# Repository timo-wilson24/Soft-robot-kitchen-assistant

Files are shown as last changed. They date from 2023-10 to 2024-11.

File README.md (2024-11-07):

# Soft-robot-kitchen-assistant
This is a repository for the code, CAD and assembly information for the 'Soft Robotic Kitchen Assistant for People with a Fine Motor disability' project I completed. 

The project addresses the challenge of food preparation for individuals with fine motor control difficulties or limb amputations by providing a dual-mode (soft and rigid) robotic device. The device uses a PneuNet based 'finger' actuator designed for finer slicing and rigid second system with some compliance. The innovation extends the applications of soft robotics and facilitates independent living for individuals with disabilities and showcasing the synergy between pneumatic rigid and compliant robotics in enhancing daily tasks. 

## Videos of Project:
- AUSSEF - Chopping Board Assistant Submission Video (recommended): https://youtu.be/T2KDRH2tRoQ?si=e9xJF4VDxiq_ELAp
- Soft Robotics Toolket Competition - Soft Robotic Chopping Board Assistant Submission Video: https://youtu.be/luMKAHcBeGc?si=Hu5qlbttlR9tySVy
- Young Scientist - Chopping Board Assistant Video: https://youtu.be/AkrwtVQIluE?si=esvOkE4GFkxM-J67

## Research Documentation
[Research documentation](Research%20Documentation/) has been formally published to the Harvard Soft Robotics Toolkit website and this repository. See
[AUSSEF Research Documentation](/Research%20Documentation/Research%20Documentation/AUSSEF%20Submission%20-%20chopping%20board%20innovation.pdf)
and
[SRT Competition Documentation](Research%20Documentation/Soft%20robotic%20kitchen%20assistant%20-%20SRT%20Submission.pdf)

## Competition Results
- 1st place in the College Category for the [Harvard Soft Robotics Competition 2023](https://softroboticstoolkit.com/competitions/2023#)
- 3rd place in the Technological Innovations Y11-12 Category at the [STANSW Young Scienist Awards 2023](https://viewer.joomag.com/2023-stansw-ysa-presentation-ceremony-booklet/0514268001701144660/p31)
- 2nd Place AARNet Use of Technology Award - Secondary ([at the STANSW Young Scientist Awards 2023](https://viewer.joomag.com/2023-stansw-ysa-presentation-ceremony-booklet/0514268001701144660/p41))

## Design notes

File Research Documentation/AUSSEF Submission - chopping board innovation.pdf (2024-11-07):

# DESIGN METHODOLOGY FOR A SOFT ROBOTIC INNOVATION: ADVANCING KITCHEN INDEPENDENCE AMONG INDIVIDUALS WITH FINE MOTOR DISABILITIES

## An Engineering Research and Development Project

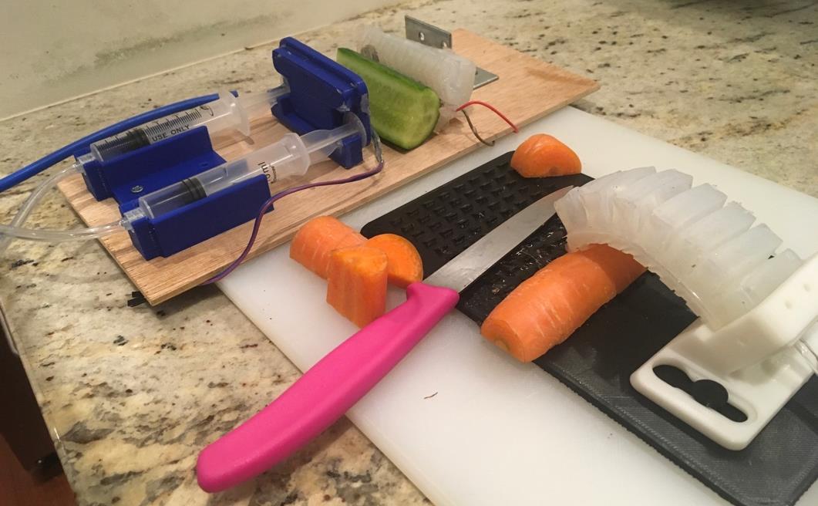
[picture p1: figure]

1. RESEARCH PROBLEM | 2
1.1. DESCRIBES A PRACTICAL NEED OR PROBLEM TO BE SOLVED IN LIGHT OF PRIOR ATTEMPTS OR SOLUTIONS | 2
1.2. EXPLORED EXISTING IDEAS AND ALTERNATIVES | 5
1.3. IDENTIFIES THE SIGNIFICANCE OF A SOLUTION FOR SOCIETY | 7
1.4. DEFINES THE CRITERIA FOR A PROPOSED SOLUTION | 7
2. DESIGN AND METHODOLOGY | 9
2.1. EXHIBITS A WELL-CONSTRUCTED PLAN TO ADDRESS THE NEED OR PROBLEM | 9
2.2. JUSTIFIES THE CHOICE OF MATERIALS AND TECHNOLOGIES SELECTED | 10
2.3. DESCRIBES A PROPOSED PROTOTYPE OR MODEL TO DEMONSTRATE THE SOLUTION | 12
2.4. DEMONSTRATES DEPTH OF UNDERSTANDING OF TECHNOLOGICAL METHODOLOGY USED. | 16
3. EXECUTION: CONSTRUCTION AND TESTING OF A PROTOTYPE | 19
3.1. EXHIBITS GOOD DESIGN AND PRODUCTION SKILLS | 19
3.2. HAS BEEN TESTED IN MULTIPLE CONDITIONS AND OR TRIALS | 33
3.3. USES AN APPROPRIATE APPLICATION OF MATHEMATICAL AND SCIENTIFIC METHODS | 37
3.4. DEMONSTRATES ENGINEERING SKILL TO DEVELOP A RELIABLE AND FUNCTIONAL SOLUTION | 38
4. CREATIVITY OR INNOVATION | 38
SIGNIFICANT CREATIVITY AND OR INNOVATION SHOWN IN ONE OR MORE OF THE ASPECTS OF THE PROJECT | 38
5. CONCLUSION AND DISCUSSION | 41
5.1. EVALUATES THE POTENTIAL IMPACT OF THE PROTOTYPE OR MODEL FOR ENGINEERING, AND/OR FOR SOCIETY | 41
5.2. DEMONSTRATES UNDERSTANDING, INTERPRETATION AND LIMITATIONS OF THE PRODUCT/SOLUTION | 42
5.3. DEMONSTRATES DEPTH OF UNDERSTANDING IN RELEVANT CONCEPTS, STRUCTURES AND PROCESSES | 42
5.4. SUGGESTS MEANINGFUL AND RELEVANT IDEAS FOR FURTHER RESEARCH AND DEVELOPMENT | 43
6. PRESENTATION AND COMMUNICATION | 44
6.1. ADDRESSES PURPOSE AND AUDIENCE | 44
6.2. DEMONSTRATES LOGICAL ORGANISATION OF MATERIAL | 45
6.3. HAS CLEARLY ILLUSTRATED INITIAL IDEAS AND ALL DESIGN STAGES TO THE FINAL DESIGN | 45
6.4. PROVIDES EVIDENCE OF A HIGH DEGREE OF INDEPENDENCE OF THE STUDENT | 45
7. EVIDENCE OF PROJECT, MEDIA OF FINAL PRODUCT | 45
7.1. VIDEO: | 45
7.2. OTHER PHOTOS OF PRODUCT: | 46
7.3. CAD, ENGINEERING DRAWINGS | 48
8. REFERENCES | 48

## 1. Research Problem

1.1. Describes a practical need or problem to be solved in light of prior solutions
Independence is an important part of adult life. As people get older, being independent becomes more difficult due to the effects of aging. Similarly, people with a disability define being independent as their key need in life. Independence is empowering and important for physical and mental health long-term. This project strives to enable people to obtain independence, allowing individuals to remain in their home environment by being able to prepare food at home, which is a core element to being independent.

Preparing and cooking food can be a significant challenge
for many individuals who face difficulties with fine motor
control, despite the availability of accessible cooking options. The process of preparing a healthy meal often involves precise and delicate slicing of various ingredients, each presenting unique challenges based on their texture and hardness, whether they are slippery, hard, small, or soft. Consequently, individuals with limited fine motor skills, or those with amputations that clearly result in a complete lack of fine motor control in one limb, often encounter obstacles that hinder their ability to prepare food in a manner similar to that of able-bodied individuals. See examples of conditions that can significantly affect someone’s independence on the right.

At present, many national populations around the world are aging. This means that in the future the number of people requiring assistance due to age-related illnesses is likely to increase. This has far-reaching implications and will require more assistive technology to be developed so people can continue to live on their own and not rely on carers through governmental social welfare (as there will

be too many people making it unsustainable). A demographic pyramid of Australia’s asymmetrical aging population is below.

Figure 4: Australian Demographics Data¹

1 Australia Age structure - Demographics (indexmundi.com) (https://www.indexmundi.com/australia/age_structure.html)

Figure 1: Rheumatoid arthiritis of the hands on an elderly individual

Figure 2: Finger amputation due to accident

Figure 3: Hand spasticity

An inability to prepare healthy and nutritious food (i.e., not being able to chop, slice fruit or vegetables) can have detrimental effects on diet and an individual’s sense of independence. Research on individuals who don’t (or cannot) cook for themselves demonstrates that, “Those eating home cooked meals more than five times, compared with less than three times per week, consumed 62.3 g more fruit (99% CI 43.2 to 81.5) and 97.8 g more vegetables (99% CI 84.4 to 111.2) daily. More freque nt consumption of home cooked meals was associated with greater likelihood of having normal range BMI and normal percentage body fat. … Those consuming home cooked meals more than five times, compared with less than three times per week, were 28% less likely to have overweight BMI (99% CI 8 to 43%), and 24% less likely to have excess percentage body fat (99% CI 5 to 40%).”²

It is well established that having a healthy and nutritious diet affects long term physical and mental health and is an important way of staying healthy for everyone³
. People with a disability are at a much higher risk of being affected by a poor diet⁴
, “Based on self-reported data, around half (47%) of people aged 2 and over with disability eat less than the recommended serves of fruit and less than the recommended serves of vegetables each day, and are more likely than people without disability (41%) to not meet the guidelines”⁵⁶
. This is a problem which endemically impacts, “Younger adults with disability are more likely than older adults with disability not to eat enough fruit or vegetables each day. Around half (53%) of younger adults (aged 18–64) with disability eat less than the recommended serves of fruit or vegetables each day, compared with 39% of older people [aged over 65] with disability.”⁷

At present, the market offers limited solutions to address the challenge of preparing fresh produce for individuals with fine motor control difficulties, and unfortunately, accessibility remains a significant concern. These existing solutions, with the notable exception of food processors, predominantly consist of passive devices like spikes and flexible clamps. However, their applicability is far from universal, as they often fall short in effectively accommodating the diverse array of culinary tasks and the wide range of fruits and vegetables encountered in daily meal preparation. Additionally, many of the existing devices require the use of sharp spikes, or other guides which require the knife to be close to the hand, increasing risk of injury. There is limited academic research The need for an innovative and comprehensive solution that caters to a broader spectrum of disabilities and culinary needs becomes apparent in this context.

2 Mills S, Brown H, Wrieden W, White M, Adams J. Frequency of eating home cooked meals and potential benefits for diet and health: cross-sectional analysis of a population-based cohort study. Int J Behav Nutr Phys Act. 201.

3 Siefert, K., Heflin, C. M., Corcoran, M. E., & Williams, D. R. (2004). Food Insufficiency and Physical and Mental Health in a Longitudinal Survey of Welfare Recipients. Journal of Health and Social Behavior, 45(2), 171–186.

4 “People with Disability in Australia, Health Risk Factors and Behaviours,” Australian Institute of Health and Welfare, July 5, 2022.

5 ABS (Australian Bureau of Statistics) (2018a) National Health Survey: first results, 2017–18, (http://www.abs.gov.au/statistics/health/health-conditions-and-risks/national-health-survey-first-results/latest-release) ABS cat. no. 4324.0.55.001, ABS.

6 ABS (2018b) ABS sources of disability information, 2012–2016, (http://www.abs.gov.au/ausstats/abs@.nsf/mf/4431.0.55.002) ABS cat. no. 4431.0.55.002, ABS.

7 ABS (2019) Microdata: National Health Survey, 2017–18, (https://www.abs.gov.au/statistics/microdata-tablebuilder/available-microdata-tablebuilder/national-health-survey) ABS cat. no. 4364.0.55.001, ABS, AIHW analysis of the main unit record file (MURF).

Aside from the clear social significance of my need, the device also contributes to current research on soft robotics by providing a comparison with a rigid robotic system (the clamp) and a soft system. My invention also provides yet another effective use case, with a clear methodology for others to follow. Soft robotics is a new field that integrates compliant and flexible materials into the design and fabrication of robots, offering advantages in safety⁸

, adaptability, and versatility⁹ . An example of
a soft robot is seen in Figure 5 below. These characteristics align perfectly with the requirements of my project, which seeks to provide a user-friendly, adaptable, and effective solution for individuals with disabilities that gives them independence to prepare food. By incorporating soft robotics principles, I aim to create a gripper that not only enhances accessibility but also contributes to the evolving landscape of assistive technology, particularly in applying these technologies to improve the quality of life for individuals with disabilities.

Figure 5: Soft robot

1.1.1. Design Situation
Many individuals with limited fine motor skills or amputations face difficulties when cooking and preparing food in the kitchen, especially to do with the chopping/slicing of fresh produce. Having a fine motor disability also greatly increases the risk of an accident in the kitchen because their grip on objects is often unstable or insufficient. This also impacts people with arm or hand amputations. It is important that people with a disability have access to tools which allow them to be independent and cook healthy, homemade food themselves.

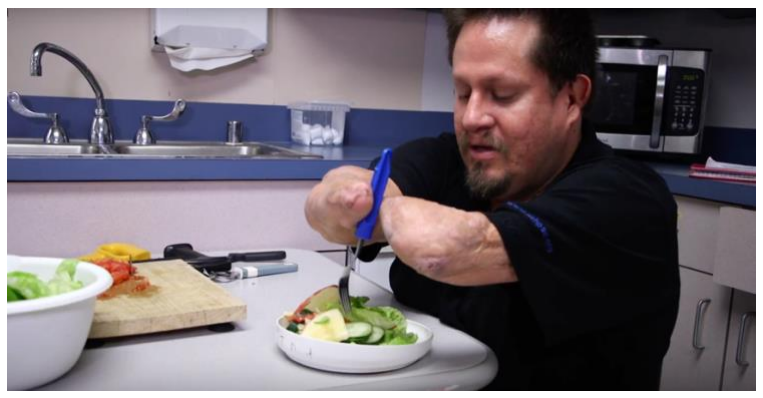
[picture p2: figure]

Figure 6: An individual with lower arm amputations making a salad. Source: YouTube

8 Haider Abidi and Matteo Cianchetti, “On Intrinsic Safety of Soft Robots,” Frontiers in Robotics and AI 4 (February 20, 2017).

9
Jun Shintake et al., “Soft Robotic Grippers,” Advanced Materials 30, no. 29 (May 7, 2018): 1707035.

1.1.2. Design Brief
Design a product which assist people with a fine motor disability to hold their fresh produce for chopping or slicing, aiming to enhance the user’s independence and effectiveness in food preparation, ensuring their safety.
1.2. Explored existing ideas and alternatives
1.2.1. Existing Product Research
To analyse existing products and solutions, I decided to research the products in categories, and ignore any duplicated products with similar conceptual design implications.
Solution 1: Safety Chopping Board Tool
- Requires two hands to use, still needs 1 hand to close the
boards holding the vegetable.
- Vegetable can still move in device (based on how hard the user is holding)
+ Very safe, well-protected
+ Easy to clean
+ Aesthetically unexciting
Target Market: elderly, those with Parkinson’s, people with limited strength, want safety.

Solution 2: Adaptive Cutting Board - Multiple devices
- Effective at holding soft objects, difficult for harder objects.
- Spikes dangerous for user
+ Good adjustability but requires some fine motor skills to move.
+ Holds most sizes of objects
+ Good modularity for future tools
+ Well planned aesthetically
Target Market: Very open to all disabilities, or people with issues prepping food. Less advertised to non-disabled audience.

Solution 3: Food Slicer Assistant - prongs

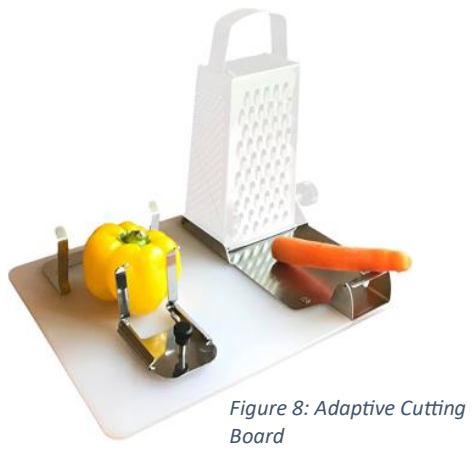
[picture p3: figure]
Figure 8: Adaptive Cutting Board

- Rounded, small diameter handle – is it able to be gripped even with a fine motor condition?
- Potential safety issue of sharp prongs
- Hard to push into the vegetable
- Only applicable to a small range of fruit/vegetables
+ Can cut between prongs and close to prongs, allowing finer slicers with safety issues
+ Very stable, little risk of fruit, hand slipping.
+ Cheap (can be found for less than $10)
Target Market: Open to the non-disabled audience, maybe chefs, or cooks generally not as good at cutting.

Figure 7: Safety Chopping Board, Source: Pinterest

Source: AliExpress.com

Solution 4: Food Processor
- Difficult to detach bowl with lid from processor
- Blades spin fast, are a little dangerous to change, clean, and put food in if you have limited fine motor
- Limited ability to slice food to a specified size.
- Decreases independence as it does it all for you
+ Handle (accessible)
+ Easy to turn on and slice
+ Does not require strength to chop (does it for you)
Target Market: Broadly accessible to all who want to get kitchen tasks done faster, and the ability to automate chopping tasks (when the user doesn’t care about precision in cutting).

Solution 5: Chopping 'Pegboard' Prototype
- Cannot hold with much force, only rest vegetables against
- Difficult to clean inside pegs.
- Requires decent fine motor skills to put in 'pegs’.
+ Adjustability for many use cases
+ Knife, utensil storage

Solution 6: Prototype 'Gear' Cutting Board
- Not much ability to hold harder vegetables like carrot.
- Product does not use a material that is easily gripped
- Cleaning is difficult.
+ Great for herbs, leafy greens as they are pushed with gears. + Operation of gears can be done with body (not hand)
1.2.2. Summary of market research

There are a few products which have been designed to assist people with the preparation of food. The current best option for people to hold while they cut vegetables is Solution 2. The solution allows individuals to use the device one handed, but it still requires a decent amount of dexterity to set up. Most user’s who require this product are going to have limited dexterity. However, this solution is not able to cater to a very large range of sizes of fruits and vegetables as well as hardness. This might mean that larger vegetables such as capsicum can’t be cut. Other solutions often necessitate the use of a second hand to use or to set up. This means that the device is not accessible for people with amputations to an arm, or stroke victims who cannot use an arm.
On the whole, the market while offering some solutions does not offer a clear solution that is adaptable to the larger target market. Furthermore, individuals with more severe fine motor disabilities are still disadvantaged significantly with most of the solutions as the operation of the device requires dexterity.

Figure 10: Common Food Processor

Figure 11: Chopping
Board 'Pegboard',
Source: Yanko designs

1.3.Identifies the significance of a solution for society
From section 1.1, it is clear that difficulties with fine motor skills have far-reaching repercussions on people with a disability’s lives because it has a big impact on their diet and health. The impact of a solution for the problem would be in improving health for a vulnerable and disadvantaged group in society, and therefore bettering social welfare. A solution that is effective would mean that people with a fine motor impairment or another disability could be independent. Socially, independence is likely to manifest in more independent housing, moving away from necessitating costly service providers in the context of ‘in home support’. An example of this is the cost of the [Australian] National Disability Insurance Scheme (NDIS) which is in place to support people with a disability. The cost per individual for in home support which might involve the preparing of meals or the assistance of preparing meals is an average of approx. $350,000 per year, per individual, across Australia. ¹⁰

The device also contributes to the soft robotic field by adding further application of soft robotic grippers to work in conjunction with people with a disability. The dual actuator design of the device also offers a point of comparison between pneumatic rigid systems and soft robotic systems, demonstrating how both systems can work together to deliver safe and effective independent living.

1.4. Defines the criteria for a proposed solution
1.4.1. Factors Affecting Design:
1. Safety – How can I make the device safe to use? What are some potential hazards to the user? Are there any potential dangers during production of device?
2. Function – What key functions must the device fulfill? How powerful does the device need to be to be useful? What are the limitations for the device functionally?
3. Accessibility – How can the device be easy to use? Can I make the controls intuitive for the target market? What would make it difficult for the user group to use the product? Are there are any disabilities that the target market might have such as vision etc.? Who are the users and what are their disabilities (stroke, arthritis, Parkinson’s etc)
4. Food safety – How can you make the product easy to clean? What materials are safe to use around food? How can you make the device hygienic?
5. Function/adaptability – What is the variety of vegetables that could be cut? How much variance is there in the size and softness is there?
6. Integration with Situation – What characterises a kitchen and kitchen devices? How can I design something which works well in the kitchen?
7. Durability – How can the device survive many uses? What materials and construction are most durable?
8. Cost – What is the price range the user group are willing to pay? How can costs of material be reduced? How can labour time be reduced? What is my budget for the project?
9. Aesthetic – What aesthetic is most appealing to the user group? How can the device look well-produced?
10. Material – What materials can be used? What materials are most durable, easy to access, food safe? Will there be any restrictions on material sources?

10 The National Disability Insurance Scheme, “Transcript for National Quarterly Performance Dashboard as at 31 March 2022” p.9

11. Maintenance – How can the components be easily replaceable? What components are most likely to fail, and how can that be mitigated? Who might repair the device?
12. Ease of use – Who is controlling the device? How will commands be inputted into the device? How will the user know how to operate the device?
1.4.2. Criteria for Success
1. Safety – The device must be safe to use. (electricity, hygiene)
2. Function – The devices should be able to hold different types of vegetables securely.
3. Accessibility – The device must be usable for people with some sight and severe motor difficulties.
4. Food safety – The device must pose no risk to food safety and should be easy to clean.
5. Function/adaptability – Most common vegetables should be able to be held by the device, and it offers some adaptability for oddly shaped vegetables.
6. Integration with Situation – The device should fit into the situation of a kitchen.
7. Durability – The device must be able to withstand 100 uses without damage.
8. Cost – The cost should be competitive and able to be bought by the user group – possibly go onto the NDIS funding.
9. Aesthetic – The design should be aesthetically pleasing and have a good finish.
10. Material – The material choices must be durable, food safe, fit the condition and be ecologically friendly.
11. Maintenance – Parts in the device must be replaceable. Parts that might often break should be easy to maintain.
12. Ease of use – The device must be intuitive with various input/control methods.
1.4.3. Target Market Definition
The target market of this assistive device is people who have difficulty with fine motor skills (limited or no control of fingers) in one or both hands.
Individual
It is hard to characterise a specific individual with fine motor
difficulties, but some individuals that have conditions that affect their fine motor skills include: elderly (often have weaker muscles, and disabilities such as Parkinson’s which limit motor control), Cerebral Palsy (issues with muscular coordination), amputees (difficulties in using and holding objects when needing two hands), stroke survivors (loss of movement/paralysis of muscles), arthritis (causes pain in joints, limited hand mobility), Duchenne Muscular Dystrophy (muscle degeneration and weakness makes holding, preparing vegetables difficult). This device appeals to their individual needs to live an independent life and cook healthy food. See characterising images in Figure 1-
3, 6, 13.
Social

The social market for this device is one centred around welfare and equity, ensuring that people who have a disability affecting fine motor can still have autonomy and independence. On a wider scale, society appreciates assistive devices as they make the lives of people with a disability better, which advocacy groups campaign for and are also useful for non-disabled people. From a government perspective, the NDIS scheme would be able to provide the funding for this device. This

Figure 13: Elderly person with parkinson's would be beneficial as this would overtime reduce the amount of carers necessary as people can live independently. Hence reducing the NDIS burden on the nation (and on individual taxpayers). Environmental
From an environmental perspective, getting more people to cook their own food and be independent leads to less food waste, healthier food (for those using the device), and reduces a harmful reliance on processed food.

## 2. Design and Methodology

2.1. Exhibits a well-constructed plan to address the need or problem
See design situation and design brief in section 1.1.1 and 1.1.2. The design brief guides the rest of the project’s intention, so that every step of the project I am moving towards achieving an effective solution to the design situation. Furthermore, a time/action plan was made to keep track of progress. The format was a Gantt chart.

Figure 14: Project Gantt Chart

2.2. Justifies the choice of materials and technologies selected
The material I chose to make the soft robotic parts from was based on academic research which investigated mechanisms of compliance in gripping designs. Silicon is most often used and can stretch considerably while maintaining a relatively low level of hardness. For my application as a stretchable and compliant gripping device, silicon has other added benefits such as its food safety and resistance to high temperatures.
Additionally, because I chose pneumatics as the method of actuation
(vs. string etc.) the best material to create the device is silicon
elastomer. Silicon elastomer comes in many different hardness’s and is sold at a few mould-making vendors. I want the gripper to be flexible against soft food, so I chose a lower hardness silicon, at about 30 Shore A (standard for this soft robotics application).
For the main body of the chopping board, the ideal material selection would be wood (aesthetics and durability), but for the prototype, I will settle for a PLA 3D Print.

Silicon Elastomer Properties: Elongation at break: 600%; Colour: translucent; Shore Hardness A: 28; Tear Strength: 20kN/m; Tensile Strength 7.5 MPa; Mix Ratio 10:1

2.2.1. Cost
Part Description | Vendor | QTY | Total Cost
Silicon Elastomer RTV3428 | Barnes | 1; 500g | $65, per unit $13
Arduino Uno | School | 1 | $25
Jumper Wires, Connectors | Jaycar | 2 | $24
12V 1A Power Supply | School | 1 | $10
Pump (one for vacuum and one for air inflation) | eBay | 2 | $31
Pressure Sensor | RS-Components | 1 | $30
Force Sensor | RS-Components | 2 | $20
Nokia 5110a Screen | eBay | 1 | $7
Rotary Encoder | eBay | 1 | $5
Solenoid valves | School | 2 | $80
Pneumatic Tubing | School | N/A | $10
3d printing filament | School | N/A | Approx. $10
Syringes | School | 2 | $10

Figure 15: A Translucent Silicon Elastomer similar to the material used in product

Part Description | Vendor | QTY | Total Cost
Screws to hold down electronics, double sides tape | N/A | N/A | $3
Wooden Chopping Board Base | Ikea | 1 | $5

Figure 16: Bill of Materials (BoM)/Cost analysis table

## Total Cost = $274

The cost of labour and other materials for this project would likely mean that one unit with all accessories would cost between $200 to $300. The cost would significantly decrease as buying in bulk for tubing and electronics would mean that postage and the unit cost would decrease.

The project relied heavily on 3D printed parts (printed in PLA filament), but the parts and moulds could all be produced in other filaments such as ABS. PLA was chosen because it is food safe, stable and cheap. It would be very difficult to reproduce or make the PneuNet designs without 3D printing technology, but some parts could easily be made out of wood or other materials (such as the chopping board). The cost of PLA filament is low and accessible for most.

The microcontroller can be changed for other similar or custom microcontrollers, but the Arduino platform is fairly cost-effective and easy to prototype. The LCD screen can be changed for another other screen tech such as OLED or a different size of LCD (or without backlight). The control of the system can be achieved through just using a laptop for prototyping or altering the code. The use of pressure sensors are necessary, and any IC pressure sensor can be used. The force sensors are non-essential and offer only a little more control. The material of pneumatic tubing can be anything that fits into 3/8” quick connect fittings, or other joinery. The transformer/power supply can be any specifications of 12V 0.5A or above DC power.

2.3. Describes a proposed prototype or model to demonstrate the solution
2.3.1. Movement Analysis (of chopping vegetables) with user group
The first stage of research to optimise the device’s function was analysing the motion and movements required for gripping/chopping fresh produce and what someone with a fine motor disability struggles with. This included video analysis, determining the most popular ways to chop vegetables and testing with user group (as a case study). The vegetables and types of chopping that I investigated included an onion, carrot, pumpkin and potato. I gathered quantitative data on the movements and the most importance of certain motions.
Results
Vegetable | Motion | Grip | Comments of User Group Performance
Onion (diced) | 1: halving (cutting lengthwise). | Holding both sides of onion | Fairly safe motion, knife had tendency to slip
| 2: Cutting/slicing into slivers | Claw grip or fingertip grip on top of onion | Confident with 75% of onion. Very difficult last 25% (fingers slipped because not enough strength to grip.
| 3: Dicing/second direction | Not holding at all or flat palm | Easy with long knife on board, thumb stuck out (safety concern)
Carrot (cut in sticks, diced) | 1: Halves (cutting lengthwise x2) | Clamp/pincer grip on both sides | Determined too dangerous for user group to test (knife can easily slip off carrot) Difficulties with strength
| 2: Cutting into chunks | Hold flat, flat hand on board | Easy to hold, no safety issues. Found sizing difficult
Pumpkin (diced) | " (same process as carrot) | " | Easy to hold, stiff, well-shaped with a less slippery texture
Potato (diced) | " | " | Large size, easy to cut in half and dice (strength/pressure) was difficult for user group

Conclusion
After analysing grip techniques required for chopping some of the most common vegetables, I have shown that there are two key movements to cutting most vegetables, no matter shape or hardness. These are:
1. Chopping the vegetable in half (using a clamp or over knife grip)
2. Slicing/dicing the vegetable in a second direction
Therefore, my design should be optimised for the above two movements.
The hardest movement was slicing the onion - especially the end of the onion (as there was little space to grip) and required much more precision. Additionally, the halving of harder vegetables like carrots and pumpkins was challenging due to strength issues and the tendency of the knife to ‘slip off’ the centre. Hence, I will try to design a device which can assist with these tasks as they are the most limiting.
2.3.2. Chosen Prototype System to Solve Problem
After ideation, research and testing, I determined that the project could be split into two central components/systems which perform two important functions of chopping/slicing vegetables. The first is a system for holding more delicate vegetables to be sliced and is completely compliant. It is based on the Harvard PneuNet design and imitates the function of a claw style grip when chopping vegetables. The second is a mostly rigid pneumatic system which has some soft robotic elements to provide compliance and mirrors the function of a clamp grip (ie. Holding both sides of a vegetable to chop in half). The control system is a 3d printed box with a screen and accessible rotary knob for both rotary and press input. Inside the box are the two pumps (vacuum and compressor), the microcontroller, the pressure sensors (receiving data from the air tubing), and valves which are used to select the device and whether to vacuum/pump.

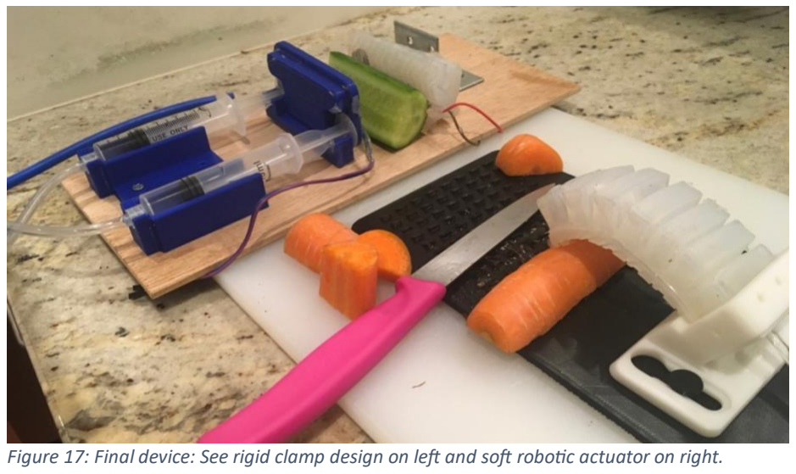
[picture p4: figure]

The manufacture and required tools are further detailed in the Fabrication/Design Process section, but the production of the device requires a 3D printer, a precise scale for measuring amounts of elastomer, cups and stirring tools for mixing, soldering tools, wires etc. and tools for pneumatic tubing such as tube cutters.

2.3.3. System 1: Soft Robotic PneuNet Gripper (biomimetic of finger)
The material that the PneuNet device is made from is silicon elastomer. Silicon elastomer is sold in varying degrees of hardness and is usually food grade. About 150g of elastomer is necessary to manufacture the device. The bending actuator is inside of a 3d printed mount which holds it in position and is slotted into a keyhole mechanism that allows the actuator to move in one axis (forward and back). This allows for securing mounting but also so that the actuator can be removed for cleaning easily and changed position for different shapes and sizes of fresh produce. The mount is 3D printed in PLA filament. The chopping board that the mount sits on can be either 3d printed (with grooves to hold vegetable in place) or can be made from a wooden chopping board. The device is supplied air pressure through silicon or polyurethane tubing. The actuator is embedded

Figure 17: Final device: See rigid clamp design on left and soft robotic actuator on right.

with a flexible force sensitive resistor (measuring compression force acting on sensor). The base of the actuator was designed to limit the slipping of the fruit through adding bumps and a textured base which meant that the fruit slips less when it is being cut.

The parameters for the size and design of the PneuNet actuator was determined through testing and prototyping various sizes of actuator. This allowed me to evaluate the weaknesses in the actuators and design custom 3d printed moulds to produce better results.

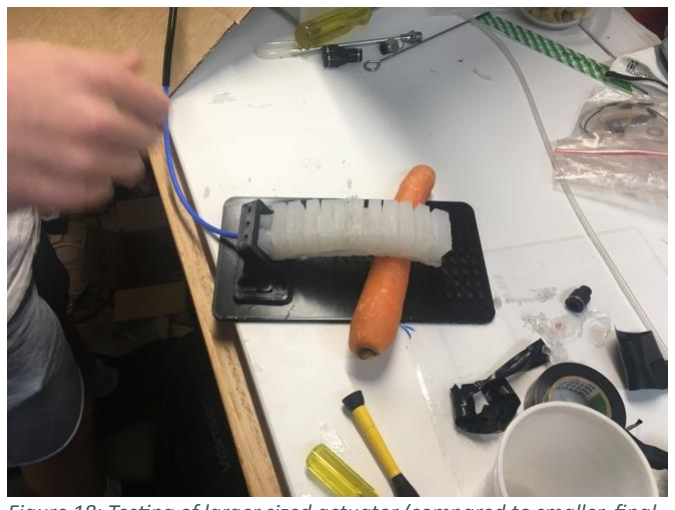
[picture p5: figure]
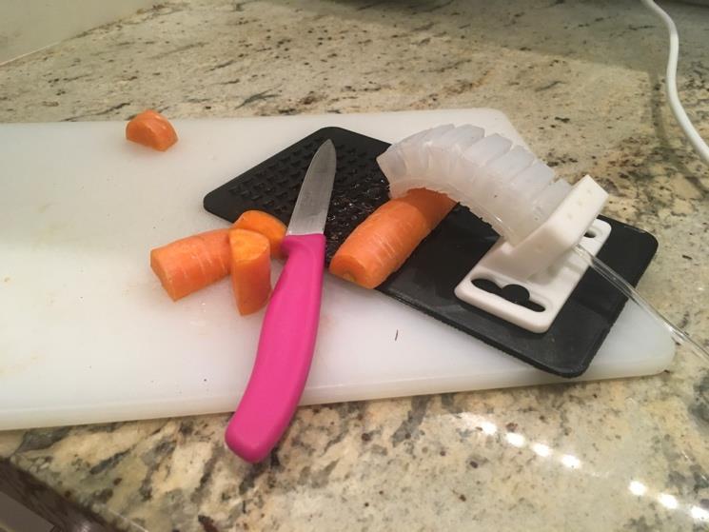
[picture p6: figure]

Figure 19: Final 'finger' PneuNet actuator on 3DP mount

Figure 18: Testing of larger sized actuator (compared to smaller, final design)

2.3.4. System 2: Mostly rigid ‘clamp’ with compliant cushioning
The clamp system is made from small syringes which act as pneumatic cylinders to provide uniform and controlled linear motion. The syringes have 10mL capacity and can be bought from some pharmacies or online. The two pneumatic cylinders (syringes) are clipped into a 3d printed bracket, which is screwed into the chopping board that holds them at a constant position with minimal/no play. The pneumatics are then attached to a 3d printed ‘jaw’ which is coated with silicon elastomer for easier cleaning and some compliance. The jaw holds both the cylinders at the same axis, so that they both extend the same amount and are not lop-sided. The other ‘jaw’ is mounted with a bracket to the chopping board and has a variation on a silicon PneuNet actuator (made in a similar method to the gripper in System 1) that adjusts the amount of compliance to not bruise the fruit and to increase the system’s safety. The jaws of the clamp also have embedded force sensitive resistors for an understanding of the forces acting on the fruit. The device’s purpose is to allow the user to cut vegetables accurately and easily in half (especially vegetables that are hard or slippery) with one hand, or without posing any risk of cutting themselves that might ordinarily occur. While fully soft robotic linear extension actuators were tested such as origami extending actuators, the devices were unsuccessful at providing sufficient force and were not as useful for this project.

Figure 20: Final clamp device (using syringes, 3DP mount). Note wires for force sensors

2.3.5. System 3: Control System
The housing of the control system is a 3D printed box, around the size of a piece of a piece of printer paper. The box was 3d printed so that custom additions to fit certain electronic components such as the screen and encoder in the lid could be easily made. The power is supplied through a singular DC in power transformer from mains which supplies 12V 1A electricity in a singular pin on the box’s exterior. There are also ports for debugging and software updating the Arduino. Along the side of the box there are two output connectors for the finger and clamp air tubes to be quickly connected and disconnected. As previously mentioned, the control of the device is done through a singular Arduino microcontroller. A breadboard is used to connect the pressure sensor, force sensors and screen to the Arduino. The small LCD screen on the box’s exterior has a GUI interface of a scrolling menu, controlled through the large and accessible rotary encoder knob. The GUI can display pressure values, force values, switch to manual vs preset mode, set the preset value and power off/on the device. This interface has been tested with individuals with limited fine motor and with individuals with an intellectual disability.

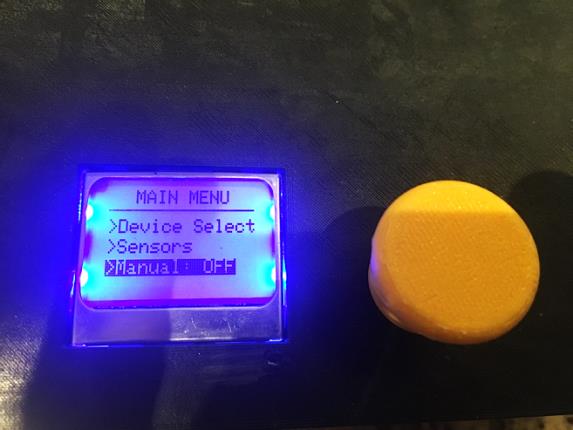
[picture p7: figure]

2.4. Demonstrates depth of understanding of technological methodology used. Relevant technical concepts related to project design and methodology referenced in project:
2.4.1. Compliance
Compliance, a fundamental engineering concept, underpins this device's functionality. Compliance allows a mechanical system to deform or yield under external forces while preserving its structural integrity. In this device, compliance is achieved through a combination of material selection and mechanical design. Flexible materials, like silicone elastomers, are strategically incorporated to enable controlled deformation when exposed to external forces, enhancing the device's adaptability and precision. Additionally, the use of pneumatic systems utilises the innate compressibility of a low-pressure gas (air) as opposed to hydraulic systems which are non-compressible.

Figure 21: Control box LCD Screen and rotary knob, top view

Figure 22: Joint and finger compliance example

2.4.2. Pneumatic Systems:
As already identified, pneumatic systems have an advantage over motorised and hydraulic alternatives as they are incompressible and hence not as safe, nor compliant and adaptable. In the context of pneumatic systems, higher pressure leads to gas compression, resulting in denser gas molecules and increased resistance to deformation. This gas behaviour functions as a spring-like element within the system, enhancing stiffness when subjected to external forces. This stands in contrast to hydraulic systems, where incompressible fluids maintain a constant volume under pressure, ensuring consistent stiffness levels regardless of pressure variations. See Figure on Boyle’s Law.
2.4.3. Feedback Controlled Systems:

Feedback control systems are a fundamental engineering concept that involves monitoring and adjusting a system's behaviour in response to changing conditions or disturbances. These systems use sensors to measure relevant parameters, compare them to a desired setpoint, and then adjust maintain the desired outcome. Feedback loops are crucial in achieving precision, stability, and reliability in various engineering applications. A feedback control system could be employed in my device to monitor and adjust factors like grip force or compliance based on real-time conditions. For instance, if the device is gripping a fragile fruit and the user has defined this, the system could use feedback from sensors to adjust grip force to prevent crushing and keep the system at a consistent hardness. This concept goes beyond compliance, as it involves dynamic, real-time control to optimize performance and adapt to changing situations. An example of a generic feedback loop is given below:

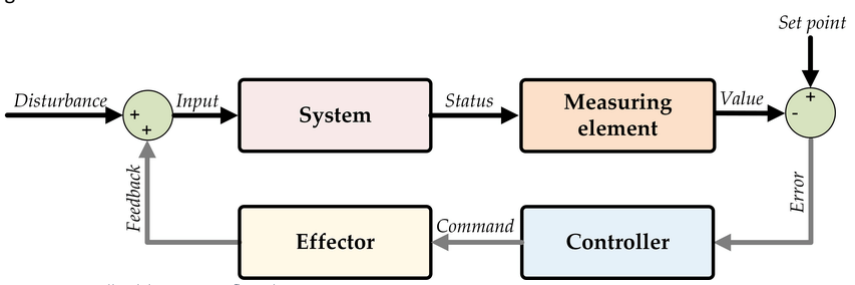
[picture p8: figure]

Figure 24: Feedback loop system flow chart

Figure 23: Boyle’s Law diagram of load on cylinder

2.4.4. Human-Machine Interface (HMI) - Graphic User Interface
In software engineering, Human-Machine Interface (HMI) serves as the crucial way of receiving information from a user and translating this into usable information for the machine to run actions and algorithms from. In this context, the manual user input from a rotary encoder provides the ability to change different factors and menus which are designed to be intuitive and easy to learn. The combination of the programming enabling the menu to function graphically in a Graphic User Interface (GUI), the software input/reading from a rotary encoder and the programming which converts this into usable variables for the other processes to run off is the HMI system.
2.4.5. Soft Robotic PneuNet Actuators
An actuator is a device that can provide force or move. Bending soft robotic actuators utilise compliance to turn pneumatic pressure (or other forms of energy) into a bending motion or compression force (on an object) which can be used to grip it. As mentioned in section 2.3.1, a bending soft robotic actuator was chosen for the first component of the design (in order to grip softer and more fine objects). There are multiple types of bending soft robotic actuators. The chosen type of design for the project was a PneuNet class actuator. These were originally developed by the Whitesides Research Group at Harvard¹¹. They consist of a series or pressurised channels which when inflated create motion. Because the underside of the actuator is inelastic, it does not stretch and therefore creates a bending motion when the top section becomes larger. The motion of the actuator can be adjusted through modifying the geometry of the chambers and channels of the actuator. Changing the inelastic, ‘strain’ limiting layer can restrict the amount of strain/motion that occurs.
The manufacture of the actuator is detailed in many research papers such as [9] from the Whitesides research group and Y. Sun’s paper characterising the class of silicon rubber soft pneumatic actuators¹²
I followed very similar methodology as to the technical construction of each actuator, detailed further in section 3.

11 Mosadegh, Bobak, Panagiotis Polygerinos, George M. Whitesides. et al 2014. “Pneumatic Networks for Soft Robotics That Actuate Rapidly.” Advanced Functional Materials 24 (15) (January 10): 2163–2170.
12 Y. Sun, Y. S. Song, and J. Paik, “Characterization of silicone rubber based soft pneumatic actuators,” (https://softroboticstoolkit.com/publications/characterization-silicone-rubber-based-soft-pneumatic-actuators) in Intelligent Robots and Systems (IROS), 2013 IEEE/RSJ International Conference on, 2013, pp. 4446–4453.

Figure 25: Example flow chart of HMI programming for a Bluetooth device

Figure 26: Diagram of PneuNet Actuator. Source: Harvard Soft Robotics Toolkit

Figure 27: Section view of PneuNet Actuator. Source: Harvard Soft Robotics Toolkit

## 3. Execution: Construction and Testing of a Prototype

3.1. Exhibits good design and production skills
Prototyping, force tests with prototypes
3.1.1. System 1: Soft robotic PneuNet Actuator
First prototype was made with information from the Soft Robotics Toolkit’s website, made of silicon elastomer and some nylon pneumatic tubing. I 3D printed two different sized moulds downloaded from the internet and tested the breaking pressure and forces generated from the two differently sized actuators. I found that for the smaller actuator, I was able to produce approx. 1.96N down (measured with a scale) and this was at 7PSI (relative). At 8PSI, the force would remain constant, and the finger would bulge outward without producing any more force. This is evidenced in the image below.

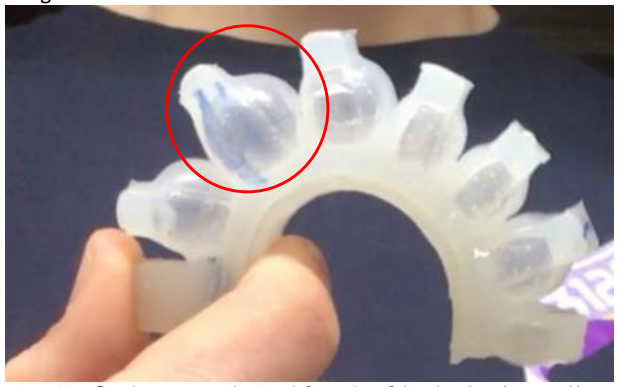
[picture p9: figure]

Figure 28: Inflated actuator, evidencing deformation of thin chambers (own work)

The larger actuator had a similar problem but at a higher pressure of 9PSI before it did not produce any additional force. At this peak, it produced approx. 2.75N of force down which was an improvement for my application. While testing this design, one of the actuators ‘bulged’ out as shown above and ruptured meaning that the prototype was no longer functional.
Design optimisation decisions:
- Reinforce the sides of the modules that inflate by increasing wall width.
- Programming: consider a ‘max pressure’ loop so that the actuator cannot burst at a high pressure
- Less length means that the actuator curls less and therefore produces a greater downward force (for this application)
3.1.2. System 2 Prototype: Soft Robotic Linear Origami Extending Actuator
Considering a method of linear extension that used soft robotics, I researched the possibilities of origami-based actuators which were based on cylindrical patterns encased in silicon. I used the principles and method from the paper “Elastomeric Origami: Programmable Paper- Elastomer Composites as Pneumatic Actuators” by Ramses Martinez et al. which included the Yoshimura origami pattern. I attempted this pattern, but found that I could not pore a mould which covered the whole paper in silicon, and the thick silicon impaired the bending of the folds and therefore caused the sides to cave in. If I chose to pursue this idea, I could investigate using a different type of paper and a thinner mould. Overall, however, this experiment led to me moving away from a soft robotic linear expansion to a hybrid pneumatic option, which has similar outcomes, but is much easier to manufacture and has great reliability.
See moulds and prototype actuator below:

Figure 30: Moulds for soft linear

actuator (3D printed, own work) | Figure 29: Origami soft linear actuator prototype (with silicon covering)

3.1.3. Fruit/Vegetable Testing (force to break)
By testing the limits of certain common fruit/vegetables I determined some of the parameters for the max force that could be applied to a piece of fresh produce that is being cut before it deforms/bruises. This was tested by hand on a scale and force was derived from the mass readout. The data is to one significant figure.
Results
Fresh Produce | Max Force Applied Before Deformation/Bruising (N)
Apple | 700
Banana | 30
Onion | 200
Carrot | 800
Pumpkin | 200
Potato | 200
Strawberry | 10
3.1.4. Design Process for Mechanisms:
Mechanism/Conceptual Ideation
As part of my research and ideation for a solution, I sketched and analysed mechanisms that could be used to solve the problem I decided on.
3.1.4.1. Simple Clamp

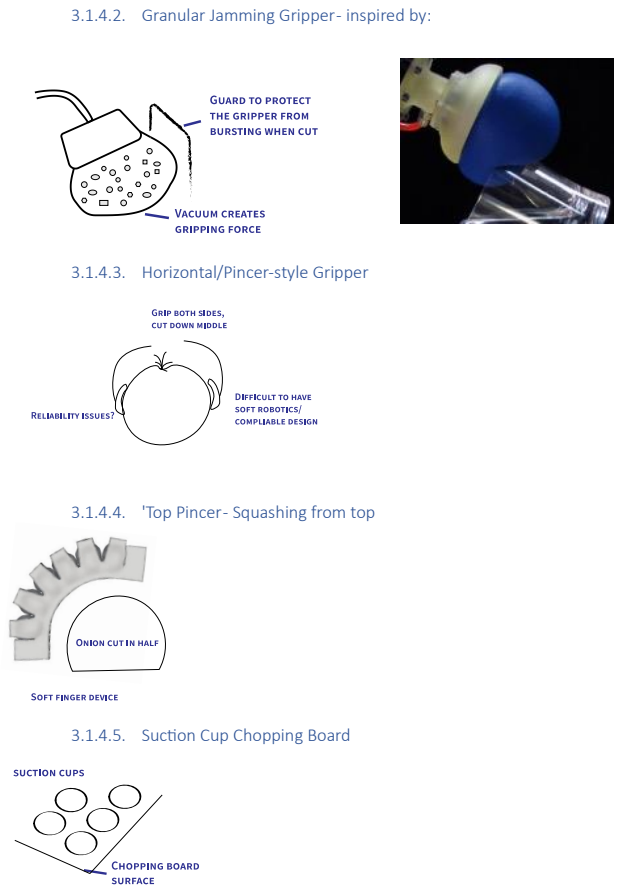
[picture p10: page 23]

3.1.4.2. Granular Jamming Gripper - inspired by:

3.1.4.3. Horizontal/Pincer-style Gripper

3.1.4.4. 'Top Pincer - Squashing from top

3.1.4.5. Suction Cup Chopping Board

Clamp:

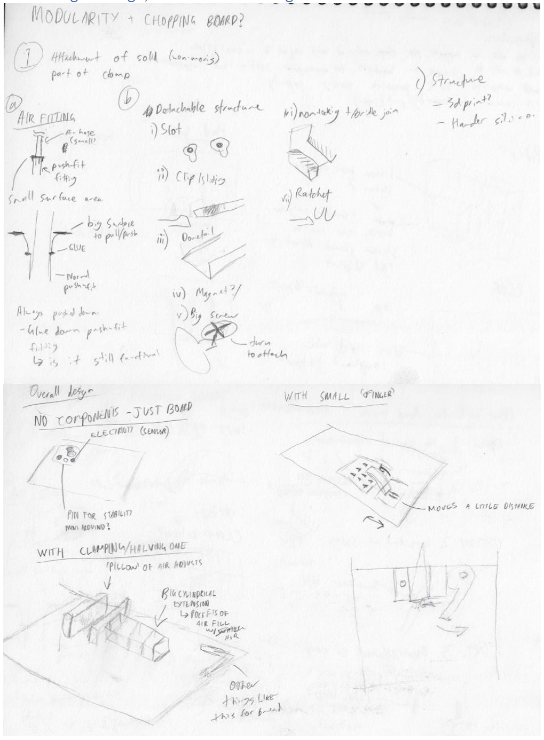
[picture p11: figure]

Finger Design, holistic device design:

3.1.5. CAD modelling (mould parts, base printable)
https://github.com/timo-wilson24/Soft-robot-kitchen-assistant/tree/1f0e81280b5753aea2adc9df44ec5698dffbd508/Solidworks%20CAD%20files (https://github.com/timo-wilson24/Soft-robot-kitchen-assistant/tree/1f0e81280b5753aea2adc9df44ec5698dffbd508/Solidworks%20CAD%20files) Once sketches of design were complete, I used Computer Aided Design (CAD) modelling to make the mould and design the board and mount, which could then be printed.
For the mould of the finger, I first made each compartment which was patterned, added air channels to make the positive of the mould. Extruding around this shape and adding tabs for mould removal completed the CAD process. By changing the dimensions of the compartments or air channels, the characteristics of the device could be altered, which was effective for prototyping. See dimensions in engineering drawing at the bottom of this portfolio.

Figure 31: Engineering Drawing of soft actuator attachment

Note air channels

Accessible knob

Figure 32: CAD design of custom accessible knob

Electronics Box/enclosure with lid

Keyed hole fits on
rotary encoder
without moving

Ribbed exterior
adds traction to
fingers, means you
can slide hand and
it still rotate.
Tactile sensation
for those who are
blind.

Generally large size
makes it more
accessible than a
regular knob

2x Electronic ports for
reprogramming Arduino
microcontroller and for
DC 12V in

(Not shown) holes for
Arduino and breakout
board PCB

2x ports for push to
connect pneumatic tubing
for each device (sensing
and control is separate, so both devices can be used
at once)

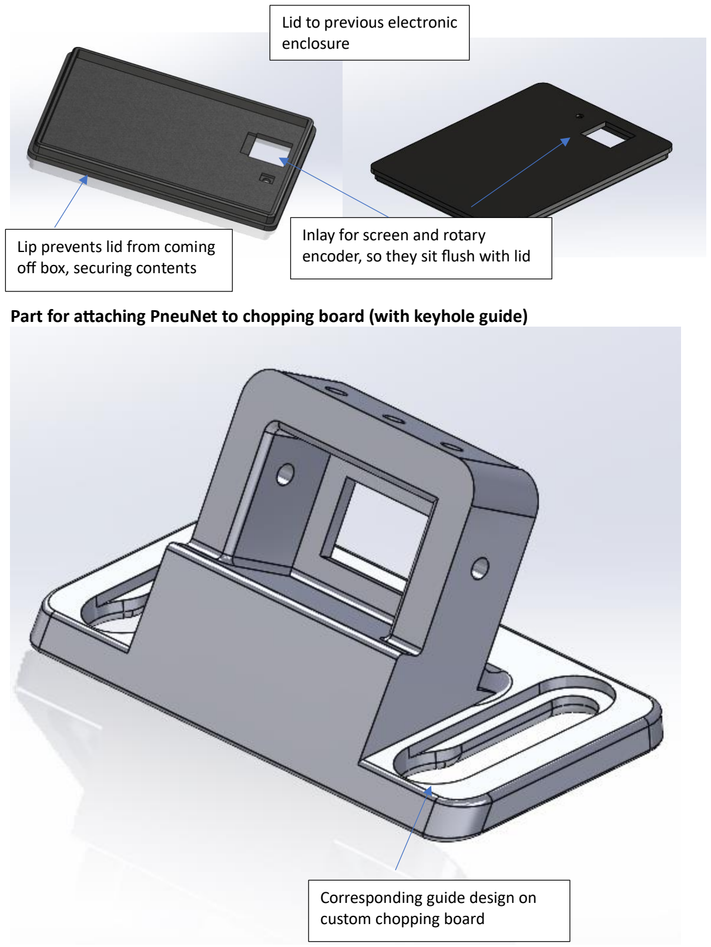
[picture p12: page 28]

Part for attaching PneuNet to chopping board (with keyhole guide)

Lid to previous electronic enclosure

Lip prevents lid from coming
off box, securing contents

Inlay for screen and rotary encoder, so they sit flush with lid

Corresponding guide design on custom chopping board

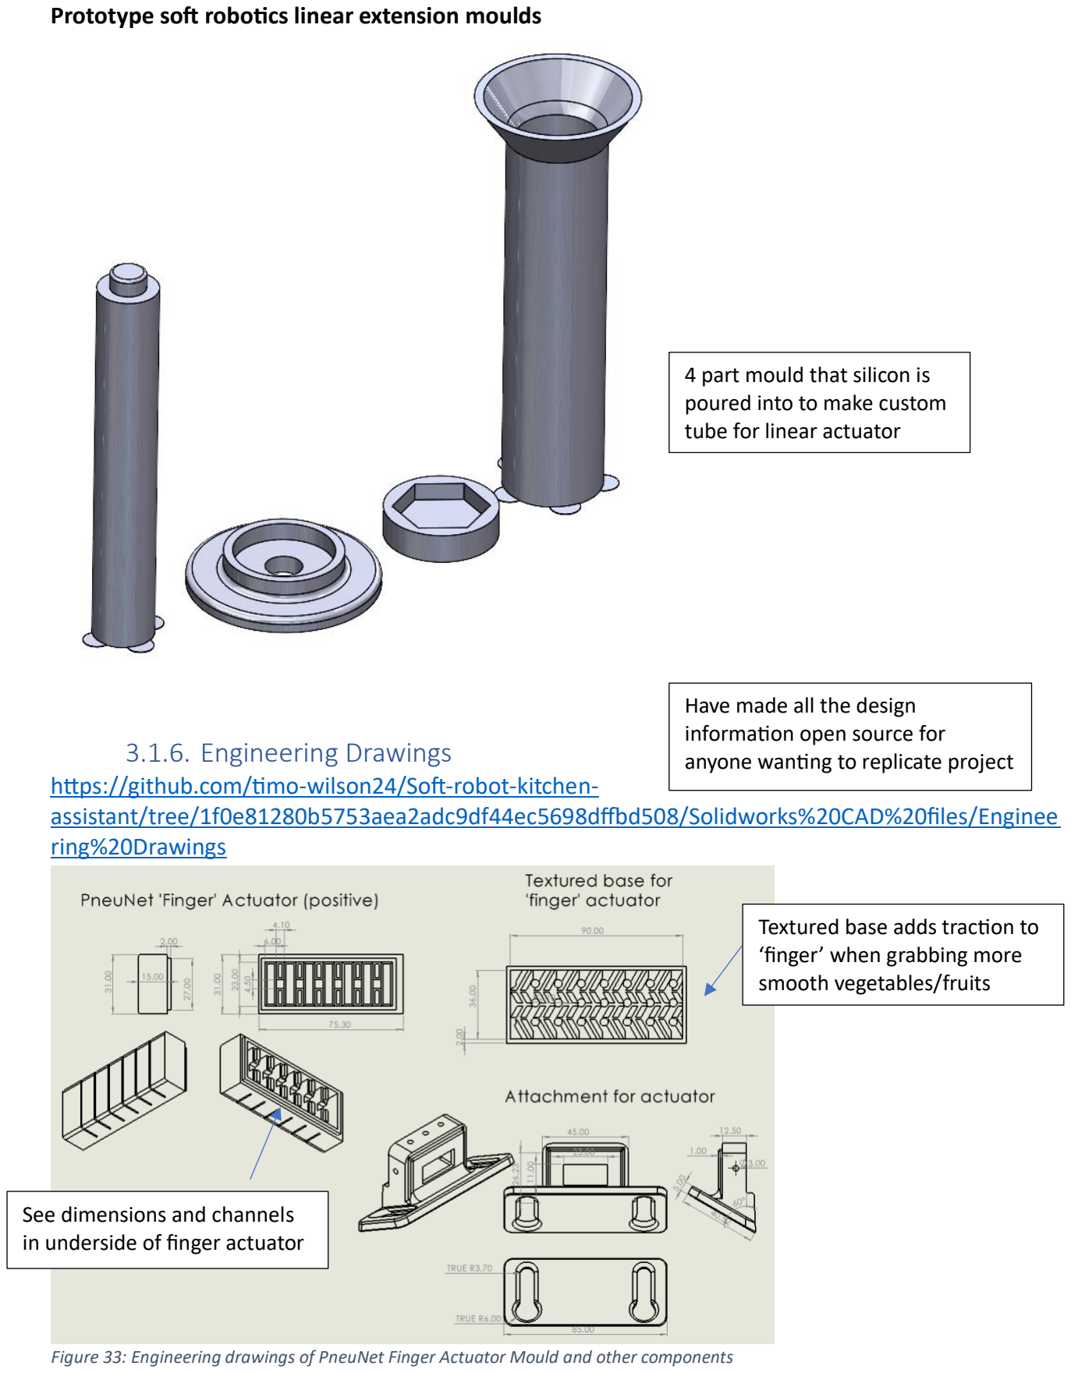
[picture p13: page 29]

Prototype soft robotics linear extension moulds

3.1.6. Engineering Drawings
https://github.com/timo-wilson24/Soft-robot-kitchen-assistant/tree/1f0e81280b5753aea2adc9df44ec5698dffbd508/Solidworks%20CAD%20files/Enginee ring%20Drawings (https://github.com/timo-wilson24/Soft-robot-kitchen-assistant/tree/1f0e81280b5753aea2adc9df44ec5698dffbd508/Solidworks%20CAD%20files/Engineering%20Drawings)

Figure 33: Engineering drawings of PneuNet Finger Actuator Mould and other components

4 part mould that silicon is poured into to make custom tube for linear actuator

Have made all the design
information open source for anyone wanting to replicate project

See dimensions and channels in underside of finger actuator

Textured base adds traction to ‘finger’ when grabbing more smooth vegetables/fruits

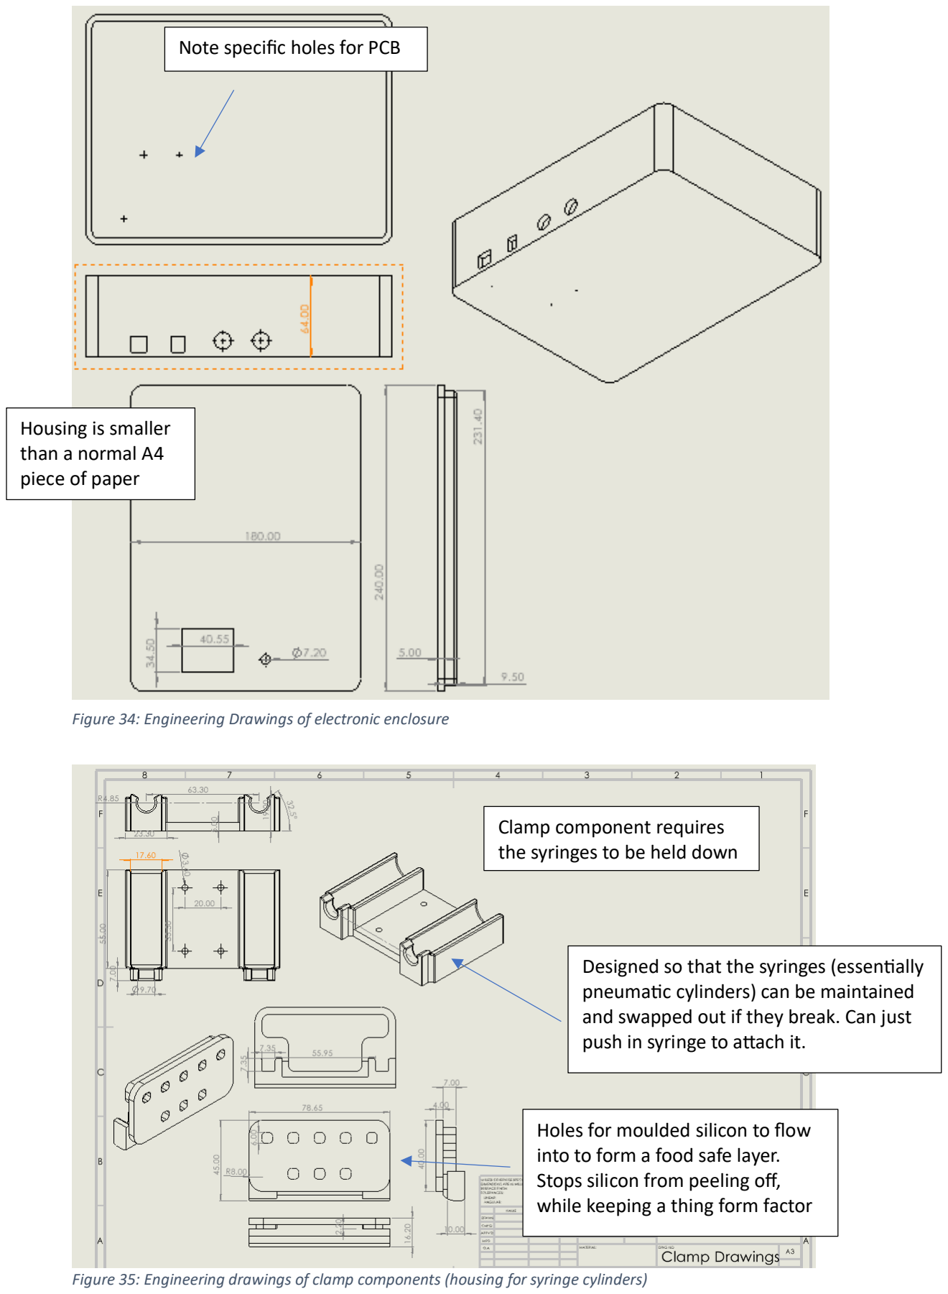
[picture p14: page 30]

Figure 34: Engineering Drawings of electronic enclosure

Figure 35: Engineering drawings of clamp components (housing for syringe cylinders)

Note specific holes for PCB

Clamp component requires
the syringes to be held down

Housing is smaller
than a normal A4
piece of paper

Designed so that the syringes (essentially pneumatic cylinders) can be maintained and swapped out if they break. Can just push in syringe to attach it.

Holes for moulded silicon to flow into to form a food safe layer. Stops silicon from peeling off, while keeping a thing form factor

3.1.7. Manufacture Process:
1. 3D printing of parts, assembly of mould https://github.com/timo-wilson24/Soft-robot-kitchen-assistant/tree/1f0e81280b5753aea2adc9df44ec5698dffbd508/Printable%20files%20(STL) (https://github.com/timo-wilson24/Soft-robot-kitchen-assistant/tree/1f0e81280b5753aea2adc9df44ec5698dffbd508/Printable%20files%20(STL)) All my prototypes and final design utilise the process of 3D printing to create customisable and highly detailed moulds for silicon. The 3D printing process involves 3 steps: slice the 3D model in a slicer software (Ultimaker Cura 5.2) using settings which make the best print quality; transfer GCODE file to a printer (Anycubic Vyper) and press print; wait for print to complete then remove 3D print from print bed with a scraper and clean model of any support material.
Once the mould is printed, the top and bottom part can be placed together, ready for silicon to be poured.

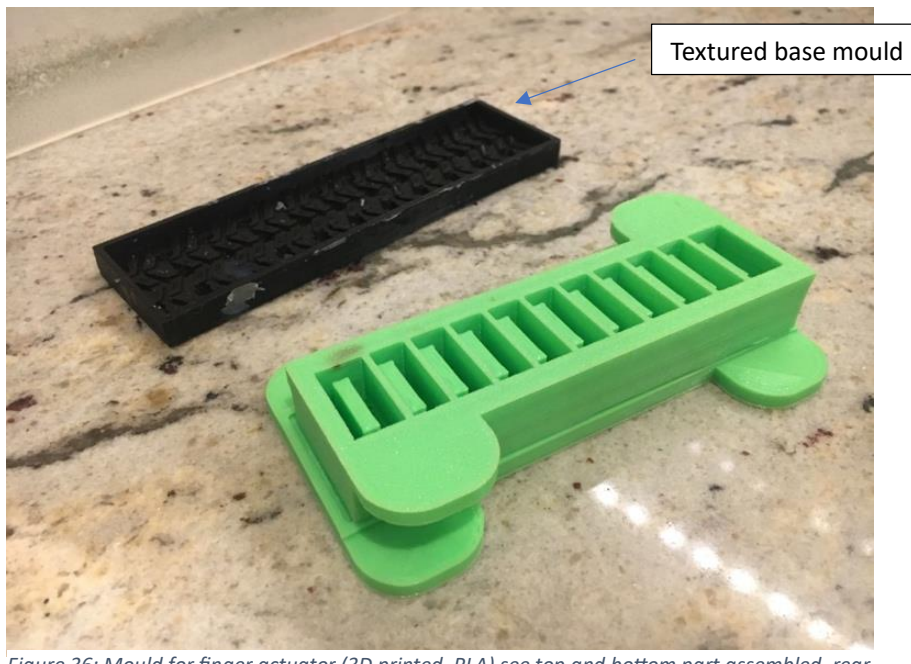
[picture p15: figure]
Textured base mould

Figure 36: Mould for finger actuator (3D printed, PLA) see top and bottom part assembled, rear is base with traction marks

Figure 37: 3D printing mould (using Anycubic Vyper)

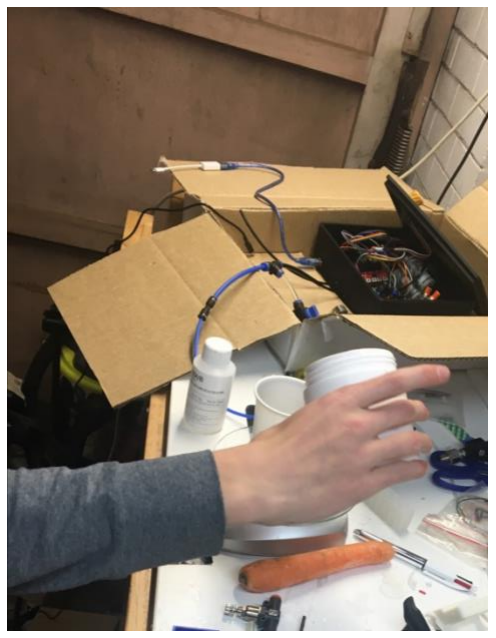
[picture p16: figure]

2. Mixing of silicon
elastomer, pouring of part 1 of mould
Mix the two parts of silicon elastomer according to the mass and the ratio given. Mix slowly and let to rest for 10 minutes to reduces air
bubbles. If applicable, use a vacuum chamber to remove
bubbles for mix. Pour the
silicon generously into the mould.
3. Insertion of Strain-Limiting Material, Curing
So that the soft robotic actuator can bend, a material (fabric or paper) must be put inside the silicon to limit its flexibility on that surface. I determined that the best durability material for this application is fabric, as paper tends to fold and crack under repetitive and high loads. Paper can, however, be used as an alternative.
Cut a piece of non-elastic fabric to place on the base (flat part) of actuator. Place on the base/flat mould once the first layer (~2mm of silicon) along with a thin flexible force sensor. Ensure the wires are accessible (either have connections or easy solder points).
4. Demolding
Use a screwdriver or other prying tool to separate the top from
bottom mould. The silicon can bend and stretch without snapping, just ensure not to puncture the walls or roof of the actuator. Once demolded, and the strain-limiting material is inserted, the top and flat part of the mould can be fused together (with more silicon), taking care as to not seal the air channels.
5. Curing

Leave parts on a flat surface for curing. Curing will take approx.. 15h. A faster curing can be achieved by leaving parts in an oven at about 50˚ -70˚ C.

Figure 38: Mixing of silicon elastomer with scales Figure 39: Pouring of silicon into base mould

Figure 40: Demolding of final upper section

6. Electronics and general assembly
Once the mechanical/soft robotic subsystems are finished, the electrical and pneumatic subsystems must be connected to the soft robotic parts. A tube must be glued into a hole punctuated in the soft robotic PneuNet device. This tube can attach to the quick connect fitting in the outside of the control box.
The pumps and solenoids (if necessary)
need to be soldered so that they can be
permanently tethered inside the box without reliability issues. The other side of the wires should be plugged into the MOSFET bank.

Connect all relevant pins to the Arduino, including the sensors. Connect the other end of the pins to the breadboard or relevant device. Solder any resistors onto the perforated circuit board.

Screw electrical components into
enclosure so that they are secured.

Attach tubing to solenoids and pressure
sensors. Attach tubing/anything else from the exterior (including the force sensor).
7. Programming of Arduino

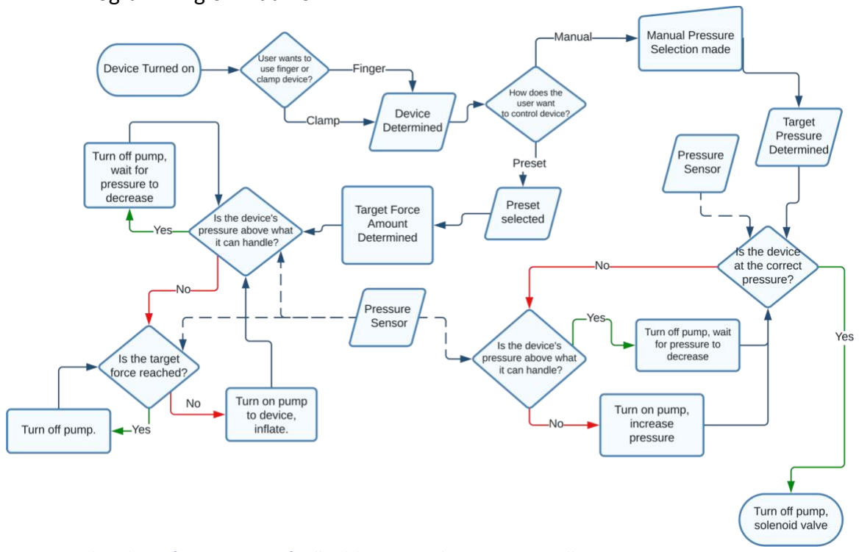
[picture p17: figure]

Figure 42: Flow chart of programming, feedback loops on Arduino microcontroller

https://github.com/timo-wilson24/Soft-robot-kitchen-assistant/blob/1f0e81280b5753aea2adc9df44ec5698dffbd508/Menu-screen-and-control-code.ino (https://github.com/timo-wilson24/Soft-robot-kitchen-assistant/blob/1f0e81280b5753aea2adc9df44ec5698dffbd508/Menu-screen-and-control-code.ino)

Figure 41: Assembly of electronics, programming of arduino in progress

I have open sourced all code I made in the

3.2. Has been tested in multiple conditions and or trials
3.2.1. Durability Experimentation
To optimise the durability of the device, I did a repetitive trial of the soft robotic ‘finger’ actuator. A program was used that counted cycles from 6PSI to 1PSI (relative) as this is about the working pressure of the device. I recorded 45 cycles for the larger device (first prototype) until a small air leak came from an air bubble in the silicon. Aside from the minor leakage, which was fixed with tape, there was some shape deformation over time which caused its rest position to be more inclined.

Factors to improve durability:
- Minimise air bubbles in manufacture of device
- Shape deformation -> vacuum feature of device to make actuator rigid and straight upright Final product durability evaluation
The test was repeated for the final design, and 100 cycles (@1-6PSI) were recorded without any leaks (due to improved fabrication quality). There was some shape deformation, but it was still usable due to the vacuum feature which pulled device to horizontal. The pressure sensor had .8 PSI of offset which could be addressed by adding a reset button for the offset to the menu, but this amount is within the functional range of the device.
The clamp part of the device survived with no change for >100 cycles, likely because of its rigid design and limited complexity. The pump and motor also remained healthy, with no variation. Results
Devices | Cycles before issue or significant deformation (@6 PSI to 1 PSI)
Prototype (1st iteration) soft ‘finger’ actuator | 45
Prototype (2nd iteration) soft ‘finger’ actuator | 60
Final soft robotic ‘finger’ actuator | >100
Clamp device (rigid) | >100
Pressure Sensor | 100
Pump | >100

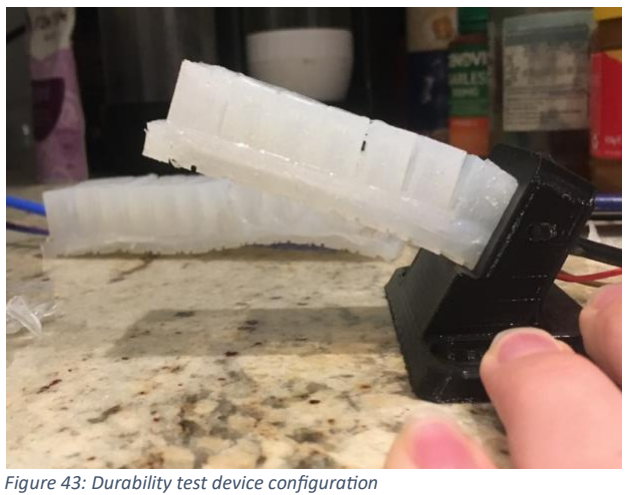
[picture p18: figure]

Figure 43: Durability test device configuration

Configuration of
device for
durability test

3.2.2. Case Study 1: Grace (with Downs Syndrome)
The case study was performed with ‘Grace’ who has Downs Syndrome and so has decreased fine motor control in her fingers and an intellectual disability. I observed her cutting some vegetables to prepare a healthy pasta, including onion, carrot and potato. This revealed the difficulties faced by people with motor disabilities in preparing food (see full results in Section 2.3.1, especially relating to safety issues around the knife slipping into fingers and potentially causing injury).

After the product was fabricated, I conducted another observation experiment with Grace to test her improvements in using the device. I explained to Grace how to use the product and she seemed to understand how to operate the screen well and increase, decrease pressure. In using the clamp system, she attempted to prepare the same vegetables tried previously without the device. While using the clamp system, her grip and cutting was much more stable than previously. She had better control over her cuts because she could focus more on the movement hand that was cutting (rather than holding the

vegetable). The only issue with the clamp device was that she instinctively felt that she had to hold the chopping board or hold the clamp to secure the device, so some suction cups should be added to the base to make it more stable.

The device held the carrot very securely and had no
movement of the carrot when slicing horizontally to
slice it into pieces. It was noted that having a very high pressure on the device made it difficult for the user to chop the vegetable as it compressed the vegetable onto the knife. A lower pressure was preferred for vegetables that could be held at a high force even though it might create some minimal movement. The clamp was also good for slicing perpendicular to the carrot to dice the carrot (if necessary). The prototype used for this test was mounted on a small chopping board which made the use of the device a little clumsy, and a larger
chopping board was used for the final prototype.

The slicing of the onion in the clamp device was

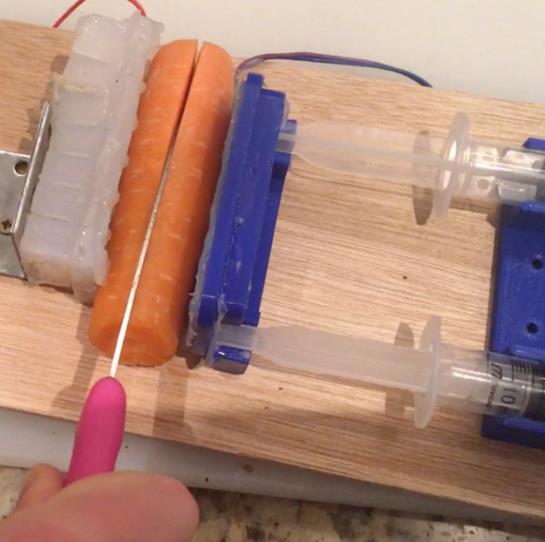
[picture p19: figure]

effective and easy for the user. The removal of the vegetable to chop it into quarters was simple as all it required was the turning of the accessible knob. Similarly, to the carrot, a higher pressure made it difficult to chop the onion in half, so a moderate pressure was preferred. It was still sometimes difficult for Grace to cut directly down the middle, so a moving guide might be considered for another prototype/future improvement.

The cutting of a more delicate fruit – a tomato – was performed to test the device’s effectiveness at all types of fresh produce The finger device was used to finely chop a tomato and it was mostly effective. It had a quite secure grip on the tomato, but it would occasionally slip. The not perfectly ideal compression force is because the curling of the ‘finger’ pulled the tomato towards the actuator base and reduced the
force holding the tomato in place. The finger
had to be used at close to its max operating

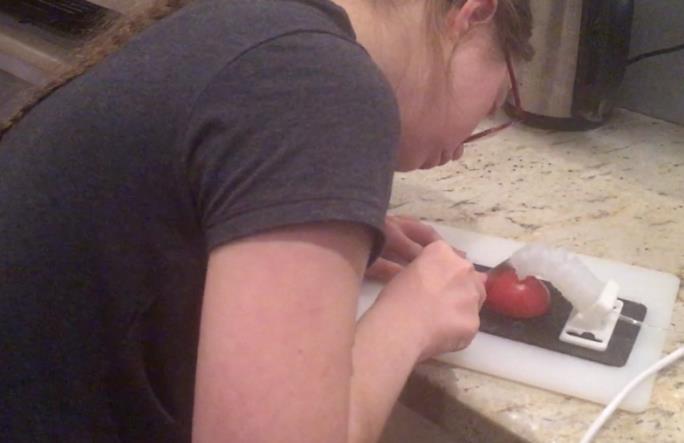
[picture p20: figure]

pressure to generate enough force to hold the tomato securely. The last section of the tomato was difficult to cut as the actuator slightly covered the last part of the fruit. This allowed Grace to finely slice the tomato for a healthy meal!

This was also trailed with the clamp device which worked fine on a low pressure and did not squash the tomato. As the tomato was easy to slice into, it was not hard to use in this setting. There were no safety concerns. Cutting the tomato with the soft actuator was effective as the device was more effective at a lower pressure.

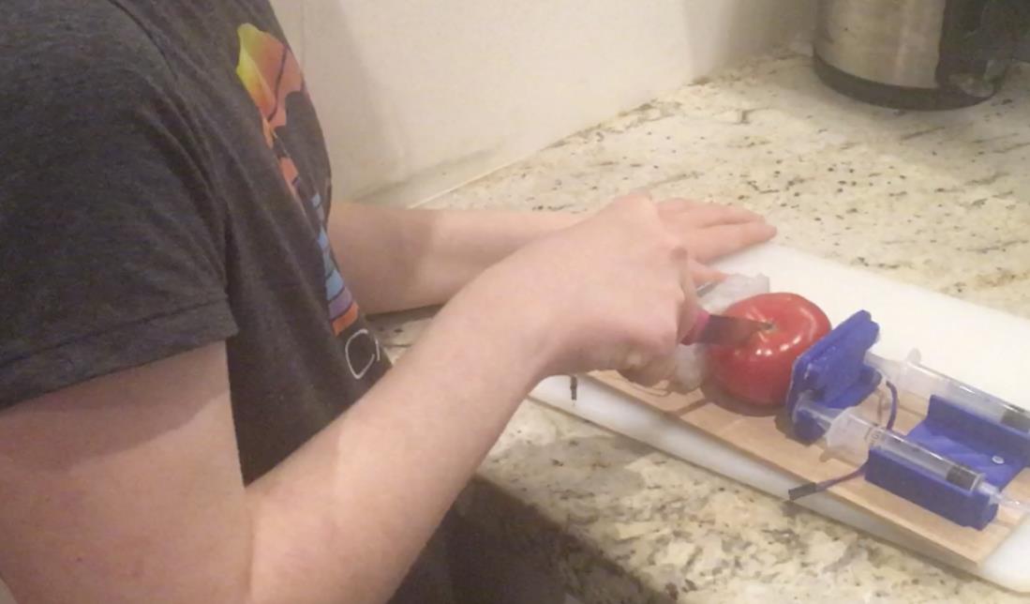
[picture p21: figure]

3.2.3. Case Study 2: Telma (eldery person with fine motor difficulty and severe macular degeneration, also have arthritis)
Before doing any observational work with Telma, I conducted an interview to hear from her as to her issues. Here are some of the answers (paraphrased) that she provided about her experiences with fine motor and sight difficulties in the kitchen and how it has impacted her.
- I am 94 and have quite a bit of pain with my arms and shoulder. I cannot raise my shoulder, so everything in my kitchen needs to be low. It hurts to push too hard into vegetables as the shoulder is in pain. [I presume she has a form of arthritis in her shoulder, though this was not mentioned].
- I often cut myself when making food as my fingers are not so good. Because it is hard for me to see, I can’t tell where the knife is and what size I am cutting. [She showed me the cuts on fingers].
- I make a lot of vegetables and mostly cook for myself, but it is still very hard to do sometimes. I have carers who help me out with other things, but they aren’t here long enough to cook everything for me. Recently some simpler meals like porridge have been better as they are easier.
- I want to continue living on my own and I like living independently and on my own.

While with her, I asked her to cut some of the vegetables
that she would normally prepare. This included a carrot, a
cucumber, an onion and some beans. The video of her
cutting in seen in my final video, see section 7.1. She used a very small knife with a small blade as it was easiest for her to hold as she had arthritis in her fingers. As she could not see the knife, her slices were quite random, and were often very large or quite thin. This also meant that she would cut very close to her holding hand without realising. More than once did she touch the knife to her ‘gripping’ hand and very nearly cut herself. This was compounded with the fact that she would sometimes shake a bit when trying to hold something carefully. Note her cutting style on the right. She was not able to cut through the carrot horizontally to make smaller carrot sticks as she was not strong enough and the
knife wouldn’t cover the whole carrot, so it would slip off.
This was also a challenge with the cucumber.

The cutting of the carrot was significantly easier with the device. This was because both hands could be used to guide and push down with the knife, so her strength improved. This also caused less pain on her part, as her right shoulder did not have to bear all the strain. Because of her poor eyesight, the sizing of pieces was still not very consistent, but it was easier for her to manage the knife and cut. In terms of safety, there was a vast and consequential improvement by using the device. It meant that even if the knife didn’t cut close to the end, it did not risk cutting her hand as it had before. She was confident to cut without her hand close to the knife. There were no safety risk as she removed the chopped vegetable from the device also.

Despite being unable to cut the carrot horizontally before, by having the carrot in the clamp device, she was able to cut through it and was very proud of herself. She was able to use a larger knife as

Figure 44: Telma cutting a carrot (very close to her fingers!)

she could use both hands, and the device held it much sturdier than she had previously when attempting to cut it herself. The cucumber was also significantly easier and she made an almost perfect cut down the middle. This was helped by using the side ‘jaw’ of the clamp device as a guide for her hand so that she cut straight.

3.3. Uses an appropriate application of mathematical and scientific methods
Used of scientific experimentation throughout the project, such as in section 3.2.1, 3.1.2, 3.1.3. The device also used a feedback loop control system to effectively monitor and determine … The use of mapping in the programming of the device meant that the pressure and force sensors were mathematically scaled to a linear graph, so that they are in a useful range and gradient. The mapping uses a function determined through the C++ code. An example of this is:
FSRval1 = map(FSR_value, FSRminForce, 1024, 0, (FSRmax + 1));

The above example maps the value for the force sensor, ‘FSR_value’, where the domain is between the variable ‘FSRminForce’ and the max for the sensor which is the largest 10 bit no. 1023 (1 is added to make 1024 as the domain is exclusive). The range of the function is defined as between 0 and the variable FSRmax (again 1 is added as the range is exclusive). The resulting FSRval1 is then a mapped value that is going to always be less than ‘FSRmax’, essentially constructing a function to return all values in that domain to be in a corresponding linear range based on the defined limits.

Utilizing the Harvard Design Process, I began by outlining the problem, drawing on scientific and mathematical data for a comprehensive analysis. This data-driven approach informed the ideation phase, where I employed mathematical models and scientific methods to generate and refine potential solutions. Throughout the iterative process, I consistently applied mathematical reasoning and scientific methodologies, ensuring a robust framework for problem-solving. Ultimately, this methodical approach resulted in a solution that effectively addressed the problem while demonstrating the practical application of mathematical and scientific methods in this project.

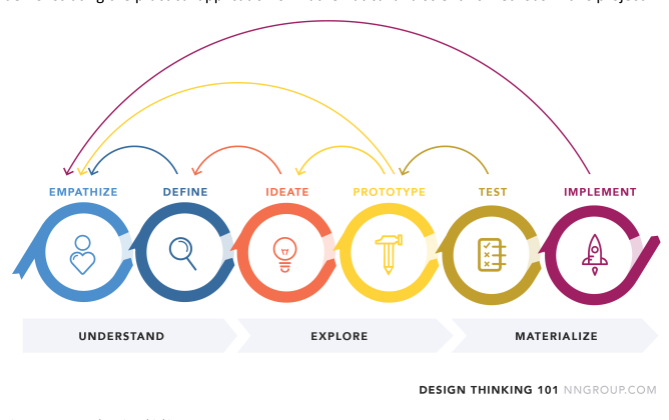
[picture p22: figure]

Figure 45: Harvard Design thinking process

3.4. Demonstrates engineering skill to develop a reliable and functional solution
The use of CAD, 3D printing, mould making and programming evidence engineering skill that makes this project an effective and functional solution. Furthermore, the improvement of the design through continuous experimentation also demonstrates engineering skill, especially given that the final product has improved on many of the factors originally designed for. The reliability of the solution is seen in section 3.2.1 and the functionality is both seen in the video (see section 7.1) and in the case study trials. The use of prototyping and testing of novel and innovative engineering design in the soft robotic components of the project is representative of significant engineering skill. The manufacturing process which produced a very functional solution is seen in section 3.1.

## 4. Creativity or Innovation

Significant creativity and or innovation shown in one or more of the aspects of the project
4.1.1. Individuality in Design Situation
Accessible devices is a large sector of the disability product market, and is popular among people with a disability as they help cater to their specific needs, also helping them to function independently. Despite this, not much care has been taken to reconsider the approach of the commercial sector. This leaves many people with a disability with minimal options. This problem is equally poor if not worse in the academic field where there is a greater bias towards disability rehabilitation, but less focus towards designing tools to assist people with their current living conditions. Elderly people are most affected by this, as there is often very little chance of their rehabilitation of disabilities. This is because most affecting disabilities worsen with age such as arthritis, macular degeneration etc.
Therefore, people with fine motor difficulties in the kitchen often do not have access or do not know about any solutions that they can access to help them. Additionally, there are rarely solutions that cater to their individual needs.
As a result of this, my project is unique and innovative as it addresses a problem not commonly thought about, researched or reapproached. By solving a problem that is less addressed and unique to a specific group of people, my project is much more likely to have a lasting and more meaningful affect on society and the individuals affected.
4.1.2. Unique design choices
The choice of mechanisms and overall design that I have solved this problem with has made for an innovative and successful solution in a way that has not been done before. There are no existing solutions for this exact issue which solve the problem by using robotic gripping technology of any kind. The use of a ‘clamp’ mechanism is common, but it is mostly moved by hand and locked by closing the device. By making it fully automatic by using pneumatic cylinders, the device can hold food much stronger and with great ease for people with strength. This is important as it means that the device can be more effective for a wider audience.

Another unique feature of my chosen solution is the soft robotic gripping finger. Soft robotics is commonly used for finger rehabilitation, and for industrial grippers, but used less with accessibility as soft robotics is an emerging field. The solution is not just unique but innovative because it solves the problem more effectively than current solutions. There are limited solutions which hold the fruit ‘top down’, and even more limited are solutions which are soft and therefore pose very limited risk of injury for the user. The biomimicry of a human finger means that it is also more intuitive to use. This is relevant for individuals in the target market who also have an intellectual disability, as
making something simple and intuitive will make it easier for
them to understand how it works.

The programming and GUI is unique and provides an easy-to-use menu for the user. There are little solutions for scrollable menus with a rotary encoder in Arduino, so much of the code was self-made. By making an interface on a small LCD screen, the user has an interface which is viewable and can change many aspects of the design. There includes function in the menu such as: preset, mode, device switching, manual mode, reset all controls, backlight and sleep mode.

The ability to use my device completely one-handed makes it very unique compared to existing solutions which often require two hands to adjust or operate.

Furthermore, by making all the key mounting parts for
both devices removable the device is much easier to
clean. The finger device has a unique keyhole feature
which means it can be securely fastened and not move but can be removed by sliding it towards one end. By making this unique mounting, I have made the device easier to operate and maintain and overall, a better solution. See the design on the right.

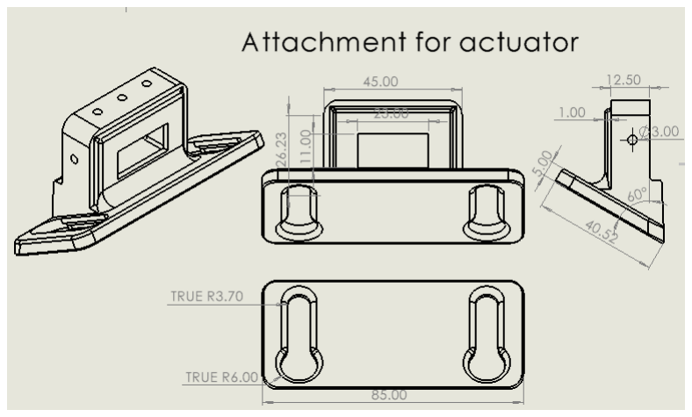
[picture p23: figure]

4.1.3. Creativity in design process (to solve problems)
Throughout the design and production of the process, I encountered many problems which required creativity and lateral thinking to overcome. The first of which was the mechanical design of the clamp component. Originally, I had planned to make the clamp device also fully soft. While prototyping a soft linear extension, I ran into problems with the folding of the actuator not functioning correctly. After doing some more trials evidenced in section 3.1.2, I decided that it was not within the scope of my project for me to design and
produce the soft extension. Therefore, I decided to
investigate how I could integrate and make a rigid
actuator safe.
I sourced some syringes and realised their potential as the actuator. To use the syringes, I designed a holder which was snap to fit, so it needed no screws or bolts

Figure 46: Evidence of device's biomimicry (source: EurekAlert!)

Figure 47: Close up of clamp device engineering drawing to assemble. This vastly reduced prototype time and makes it much easier to assemble. See design on the right.

To make this safe for the user and
so that the fruit/vegetable would
not get damaged in the use of the device, I made another soft silicon ‘jaw’ which was attached to the chopping board base. See Figure 41.

To integrate sensing into the actuators, so that I could monitor and control the amount of pressure
applied to the fresh produce, I
inlayed the sensor in the silicon

actuator. This was unique as it also allowed the sensor to double as a strain-resistant layer. This is not a process commonly used for sensing on soft actuator devices.

Figure 48: Close-up of clamp device

## 5. Conclusion and Discussion

5.1. Evaluates the potential impact of the prototype or model for engineering, applied science and/or for society
5.1.1. For Engineering, applied science
The development of this project contributes valuable insights and practical applications to the field of soft robotics, particularly in the context of assistive technology.
The integration of rigid and compliant systems, particularly in the mounting of the soft ‘finger’ actuator and the ‘jaws’ of the clamp are effective demonstrations of how soft robotics can be used to enhance rigid and more conventional robotic systems. It also offers a point of comparison between pneumatic rigid systems and compliant systems, demonstrating how both systems can be used concurrently in a solution to deliver safe independent living. In doing so, the device will meaningfully encourage other research into more modular/movable mounting for the commercial application of soft robotics.
The research and development to the PneuNet ‘finger’ actuator and rigid clamp are now open sourced, so anyone looking to prototype similar solutions or looking into optimise the PneuNet model for similar or different applications have a knowledge base and CAD files which can be used to reproduce the project.
5.1.2. Social Impact
The social impact of my device is significant. It directly addresses the practical needs of individuals with fine motor disabilities, enhancing their independence and enabling them to participate more actively in daily life, particularly in culinary activities. This has a direct positive effect on their quality of life, providing them with a sense of autonomy and dignity. In my family directly, it has meant that my sister (who has Down Syndrome) can cut vegetables with confidence and participate more in the making of her meals, rather than being too afraid to cut, or there being safety issues in her chopping of fruit/vegetables.

A functional societal should care for and assist those most vulnerable, so when fine motors disabilities significantly affect the diet of this group of people, something must be done to address this. As the device makes it easy for people with a fine motor difficulty to prepare healthy meal options, widespread use of the device will improve public health and therefore better society. At present, limited solutions address the challenge of preparing fresh produce and accessibility remains a significant concern. These devices often fall short in effectively accommodating the diverse array of culinary tasks and the wide range of fruits and vegetables encountered in daily meal preparation. The need for an innovative and comprehensive solution that caters to a broader spectrum of disabilities and culinary needs becomes apparent in this context.

Moreover, this device has the capacity to challenge prevailing societal attitudes towards disability by demonstrating the competencies of individuals with fine motor disabilities. It can play a role in shaping a society that not only embraces diversity but actively promotes inclusivity and equal opportunities for everyone. In essence, the social impact of this device spans from immediate enhancements in users' lives to the prospect of enduring societal transformation and technological progress.

5.2. Demonstrates understanding, interpretation and limitations of the product/solution
5.2.1. Evaluation of limitations relating to criteria for success:
1. Safety: The clamp component/device is strong when on a high setting, so adding another failsafe to the control system such as a second button needing to be clicked to activate higher pressure might be a good idea. A new device mode restricting max pressure more could also be explored to improve overall safety.
2. Function: The function of the clamp device is effective, but it could be improved if the chopping board it was mounted to was secured to the kitchen bench. This problem is easily solved with suction cups or a clamp fixture to the bench. The soft robotic bending actuator does not have too much compressive power which can impact the device’s performance on harder or more slippery vegetables. Making the finger apply the compressive force more uniformly downward would also assist in
3. Food Safety: There is some risk to food safety due to the open ports on the Arduino, which could get food in them and be impossible to remove. Covers should be considered. The actual device in contact with the food uses only food safe materials and has no issues.
4. Adaptability: Perhaps greater range adjustments for finger device, to make it more adaptable for taller vegetables, and for some flat vegetables such as asparagus.
5. Integration with Kitchen: Control box is quite large, so reducing the size would make it integrate more with the situation and be less intrusive
6. The cost of the production is quite high as I had to buy lots of wires, resistors etc. I think without labour costs, the product costs less than $100 which mostly fulfills my aim, but some cheaper materials should definitely be considered.
7. Aesthetics: No, the product doesn't look very aesthetically pleasing, and is instead a little obtrusive due to its current bulky size. The colour and mainly standard design means it is not ‘loud’.
8. Material: the print material is about moderate quality and could be improved with some sanding. Happy with material selection for the soft actuator
9. Maintenance: Most of the design can be easily cleaned, but making the tubing easier to disconnect from the control box would make the maintenance and potential deep cleaning easier.
10. Ease of Use: currently no second input method which for people who are blind, or for people who have no way to control the rotary knob. Some users may require a different design to the control knob such as the addition of a lever that they could push rather than turn.
5.3. Demonstrates depth of understanding in relevant concepts, structures and processes
See technical explanations of concepts, components in section 2.3, 2.4. General understanding of scientific process evident in section 1-3 and the video as I explain the process and the case study. The understanding of scientific structures and design is seen in the experimentation of the project, with multiple case studies and experiments, see section 3.2 and section 2.1.

5.4. Suggests meaningful and relevant ideas for further research and development
5.4.1. Future Research
In the future, I hope to expand on the electronic control of the pneumatic system of the device. This might mean potentially using more solenoid valves, or more reliable solenoid valves, so that there is no need to rely on any manual valves for normal operation. I think using a harder silicon material would be more effective at holding down the fruit/vegetable when using the finger device, as there is a little bit of a force limitation from the soft material bulging. Additionally, it would be wonderful to see more research done into soft robotic linear actuation with origami, as it would be a safer alternative for my clamp device to have a completely soft system (across both devices!). Lastly, some future progress could be made in more user group testing with the appliance, identifying from their suggestions the best ways to move forward with further assistive innovations. This could include better designed controls for the interface system with a larger screen, or using different input methods. This could involve voice control, larger buttons, or even a joystick.
5.4.2. Other Applications of Design
The device can be used for plenty other user groups in the kitchen – for example it could make the chopping of vegetables in a professional kitchen more efficient or safer. For fast food restaurants where efficiency and safety of (often) not highly skilled workers is key, this device could be used to minimise risks of injury. It could also help with allowing the employment of people with a fine motor disability in the hospitality industry, making a big difference financially on their lives.
In other applications aside from the clear kitchen application, the device could be used in the workshop setting for automating the holding of fine parts. This could be for electronics, where clamps and soft holders are often needed to allow for steady soldering and the attachment of parts. Additionally, the device could be scaled up to a larger workshop setting and be used as an automated clamp and holder for woodworking for people with a motor disability.

## 6. Presentation and communication

6.1. Addresses purpose and audience
As of the purpose for the project, this is addressed in section 1.1, 1.3. The purpose academically is set out throughout this paper, as I have both open sourced the paper and my results as well as clearly explaining my methodology.
In terms of the audience of the paper, concise style of the paper, along with detailed explanations of decisions will enable future researchers to be able to replicate the project and use parts of the project for future research. Additionally, the open sourcing of the project’s CAD and code allows other researchers to easily continue on my work.
The audience of the device is explained in section 1.1. To directly address those who might use or buy the device developed, there is an accompanying user manual:

Figure 49: User Manual

6.2. Demonstrates logical organisation of material
Through the ordering of material, naming of figures, and the structure of this paper with clear sections, it is evident that I have logical material organisation. The material of this paper is roughly organised using the Harvard School’s design thinking process of:
6.3. Has clearly illustrated initial ideas and all design stages to the final design
The progression of the design process is clearly detailed in the time planning and general ideation in section 2.1. Further illustration of the development of initial ideas is displayed in initial concept sketches which highlight my design thinking and early development in Section 3.1.4.

The decisions at each of the design stages are detailed and have continual evaluation in the process. This includes research (1.2-1.4, 2.4), material choice (2.2), time planning and general plans (2.1, 2.3), construction in section 3, and the evaluation of the final product through scientific experimentation and conclusion (3.3, section 5).

Further evidence of the prototype and design process are seen at the end of the video (see section 7.1).

6.4. Provides evidence of a high degree of independence of the student
The project was completed independently, this is clearly evidenced in:
- Videos made during the prototype stage (seen in the final video linked in …) . These show explanations of design process, challenges I faced and the reasons behind the final design choices.
- The research on topic (both primary and secondary) and clear explanations in other sections demonstrate understanding of concept, and display my individual and thorough design process.
- Explanation of methodology in section 2 detail a good understanding of topic and decisions. Despite the project being completed largely on my own, I would like to thank the contributions of: my parents in helping with difficult parts of construction that required two people, in assisting filming parts of the video and for their help in funding their project; and my DT teacher for helping guide me on my project path.

## 7. Evidence of Project, Media of Final Product

7.1.Video:
YouTube link:
https://youtu.be/T2KDRH2tRoQ

Google drive:
https://drive.google.com/drive/folders/1qww55SaSp3BqxEDuzN_p_HGzx8bOS1_8?usp=sharing

[In case YouTube link does not work]

7.2.Other Photos of Product:

Soft silicon
‘finger’ device,
holding carrot

Custom tactile
chopping board
with mounting
for device

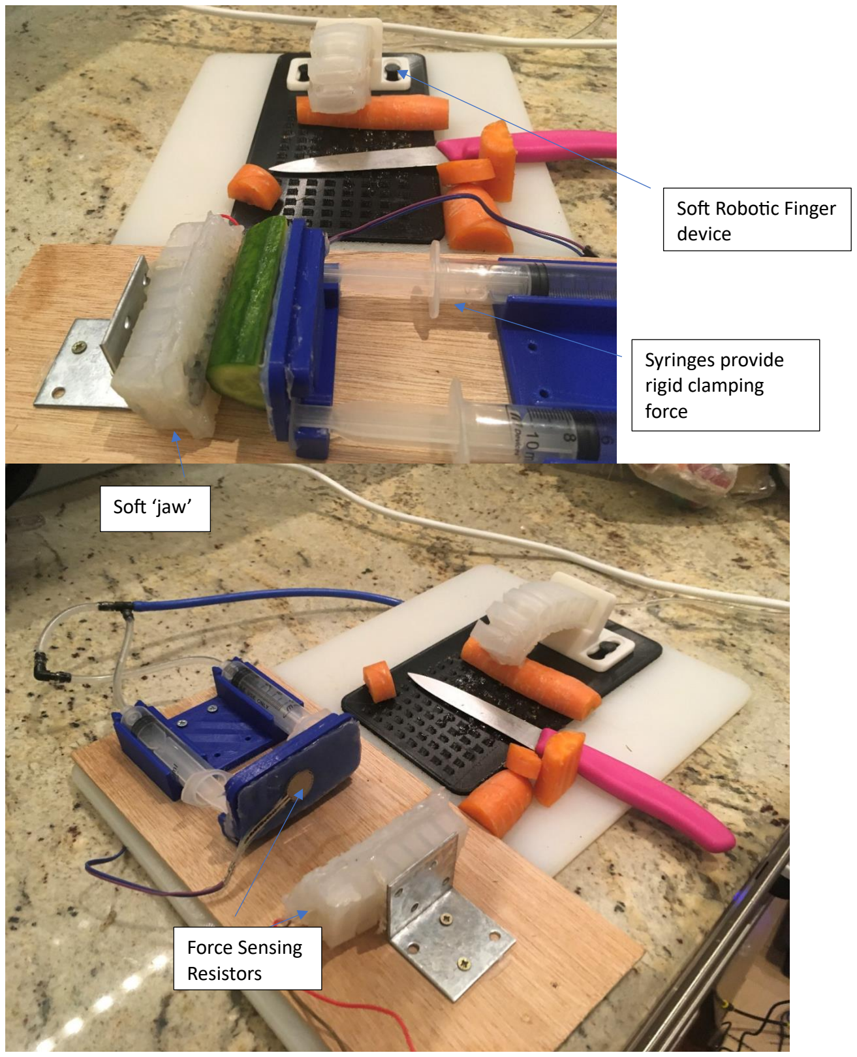
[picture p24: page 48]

Force Sensing
Resistors

Soft Robotic Finger
device

Syringes provide
rigid clamping
force

Soft ‘jaw’

7.3.CAD, Engineering Drawings

See all CAD and engineering drawings of product in section 3.1.5

## 8. References

Abidi, H. and Cianchetti, M. (2017). On Intrinsic Safety of Soft Robots. Frontiers in Robotics and AI, 4. doi:https://doi.org/10.3389/frobt.2017.00005.
Australian Bureau of Statistics (2018a). Main Features - Summary. [online] www.abs.gov.au. Available at: https://www.abs.gov.au/ausstats/abs@.nsf/mf/4431.0.55.002 [Accessed 12 Sep. 2023].
Australian Bureau of Statistics (2018b). National Health Survey: First results. [online] www.abs.gov.au. Available at: https://www.abs.gov.au/statistics/health/health-conditions-and-risks/national-health-survey-first-results/latest-release.
Australian Institute of Health and Welfare. (2022). People with disability in Australia, Health risk factors and behaviours. [online] Available at: https://www.aihw.gov.au/reports/disability/people-with-disability-in-australia/contents/health/health-risk-factors-and-behaviours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 [Accessed 26 Aug. 2023].
Iacono, T., Humphreys, J., Davis, R. and Chandler, N. (2004). Health care service provision for country people with developmental disability: an Australian perspective. Research in Developmental Disabilities, 25(3), pp.265–284. doi:https://doi.org/10.1016/j.ridd.2003.09.001. Maeder-York, P., Clites, T., Boggs, E., Neff, R., Polygerinos, P., Holland, D., Stirling, L., Galloway, K., Wee, C. and Walsh, C. (2014). Biologically Inspired Soft Robot for Thumb Rehabilitation1. Journal of Medical Devices, 8(2). doi:https://doi.org/10.1115/1.4027031.

Mosadegh, B., Polygerinos, P., Keplinger, C., Wennstedt, S., Shepherd, R.F., Gupta, U., Shim, J., Bertoldi, K., Walsh, C.J. and Whitesides, G.M. (2014). Pneumatic Networks for Soft Robotics that Actuate Rapidly. Advanced Functional Materials, 24(15), pp.2163–2170. doi:https://doi.org/10.1002/adfm.201303288.
Rus, D. and Tolley, M.T. (2015). Design, fabrication and control of soft robots. Nature, [online] 521(7553), pp.467–475. doi:https://doi.org/10.1038/nature14543.
Shintake, J., Cacucciolo, V., Floreano, D. and Shea, H. (2018). Soft Robotic Grippers. Advanced Materials, 30(29), p.1707035. doi:https://doi.org/10.1002/adma.201707035.

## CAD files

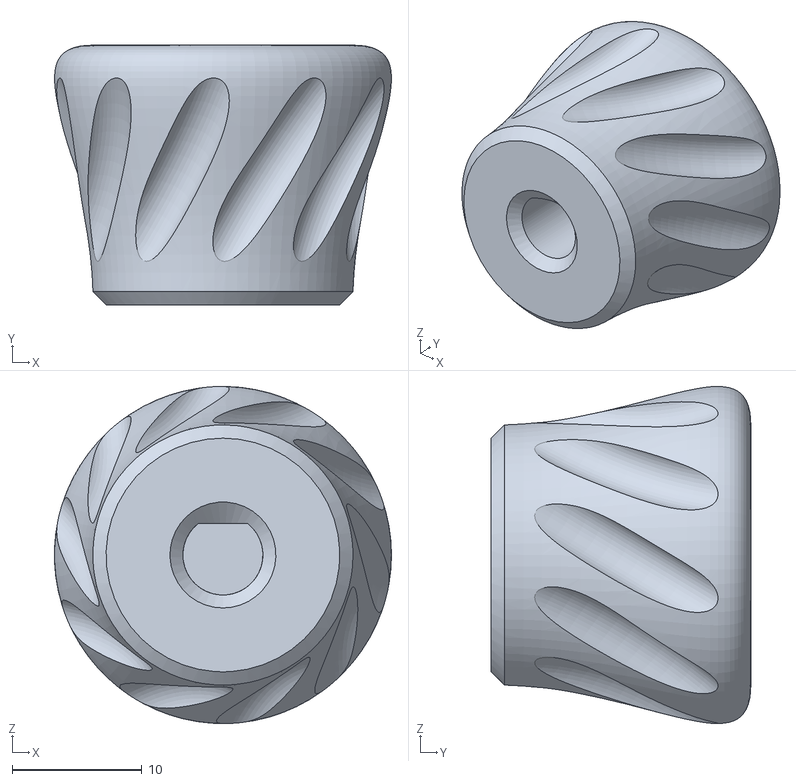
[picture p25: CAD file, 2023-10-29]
Printable files (STL)/Knob v2.STL
26.0 x 20.0 x 26.0

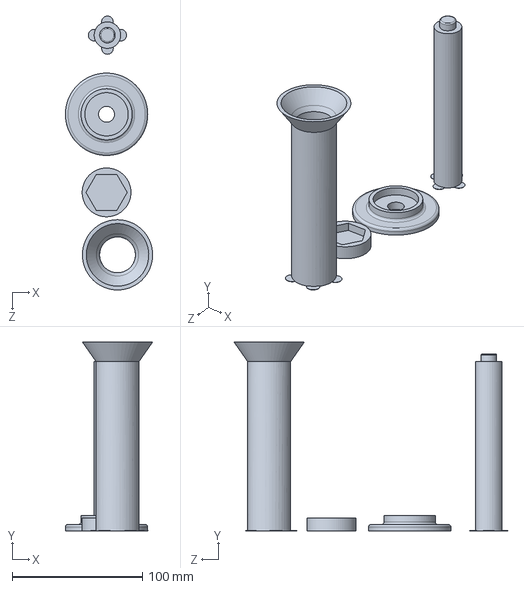
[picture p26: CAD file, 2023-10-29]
Solidworks CAD files/(PROTOTYPE) Mould for origami soft linear extension actuator.SLDPRT
67.0 x 145.0 x 210.4 mm

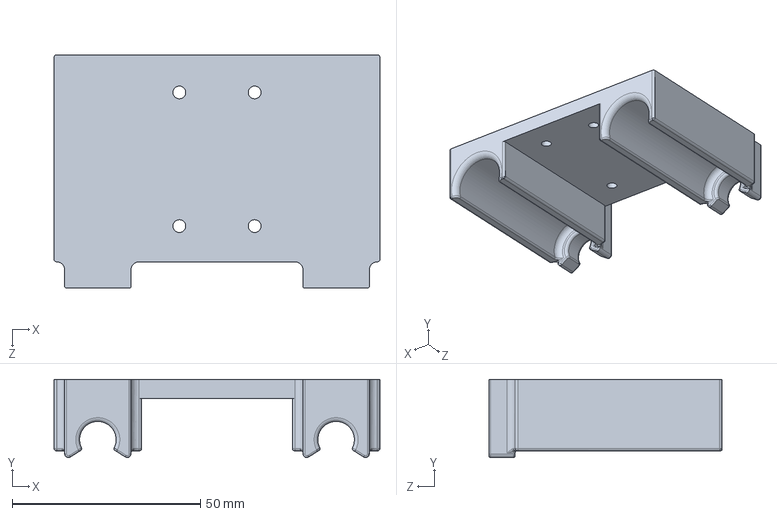
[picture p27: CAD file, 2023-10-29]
Solidworks CAD files/Clamp Device/Holder for 2x 10mL syringes.SLDPRT
86.6 x 20.8 x 62.0 mm

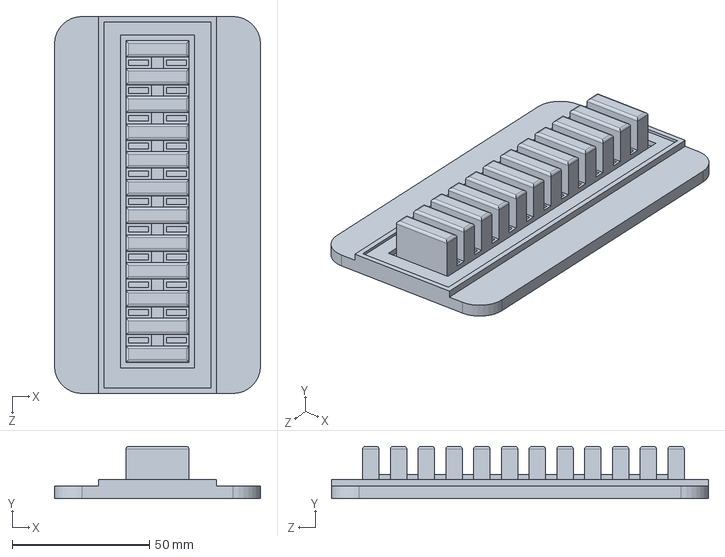
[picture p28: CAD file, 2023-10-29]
Solidworks CAD files/PneuNet 'Finger' Actuator/(Prototype) PneuNet longer length - BASE section.SLDPRT
75.0 x 19.0 x 137.2 mm

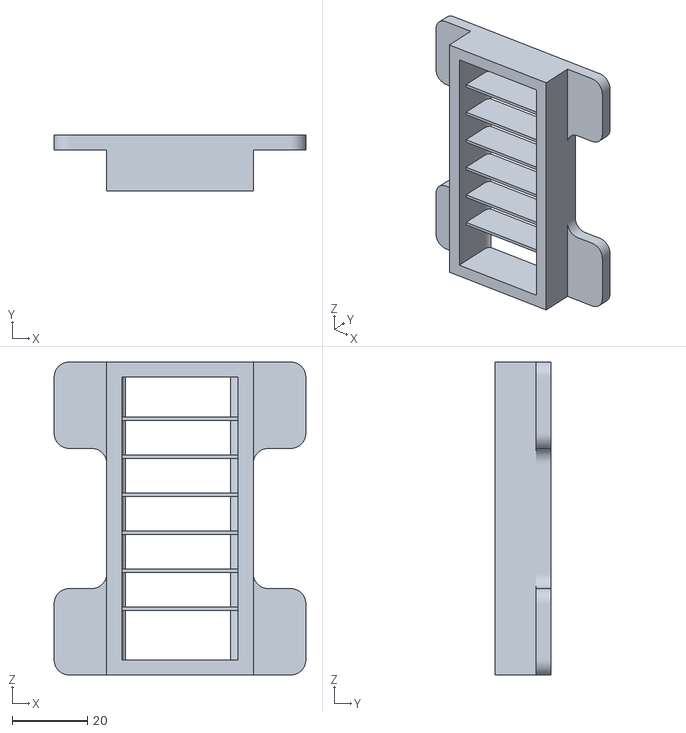
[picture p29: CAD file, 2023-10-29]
Printable files (STL)/Mold soft actuator - top.STL
67.0 x 15.0 x 83.3

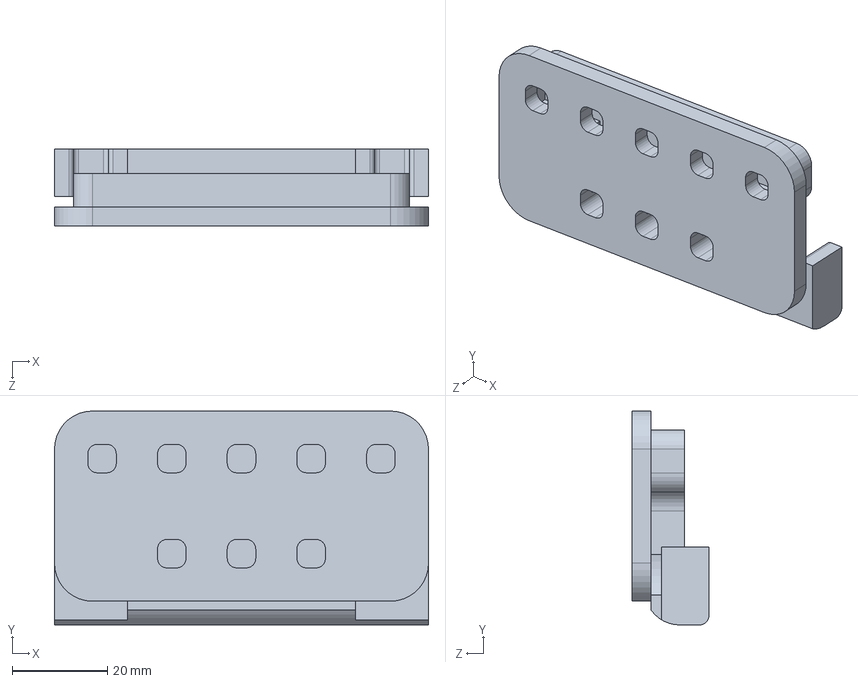
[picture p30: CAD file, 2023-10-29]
Solidworks CAD files/Clamp Device/Clamp device - Syringe-side jaw (attaches to end of syringe).SLDPRT
78.7 x 45.0 x 16.2 mm

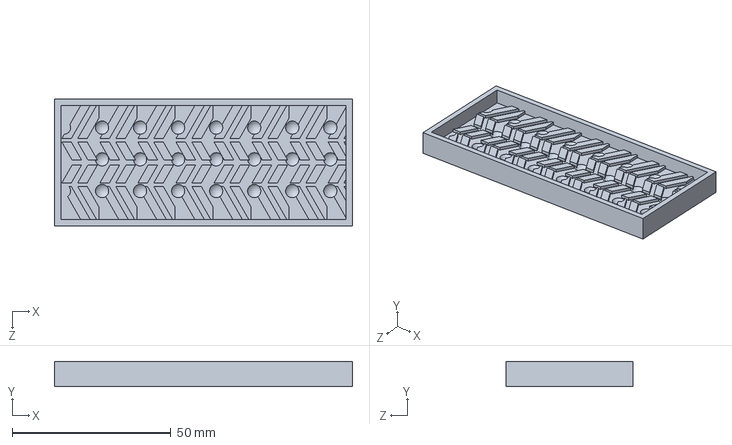
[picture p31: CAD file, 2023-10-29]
Solidworks CAD files/PneuNet 'Finger' Actuator/Textured base basic pneunet.SLDPRT
94.0 x 8.00 x 40.0 mm

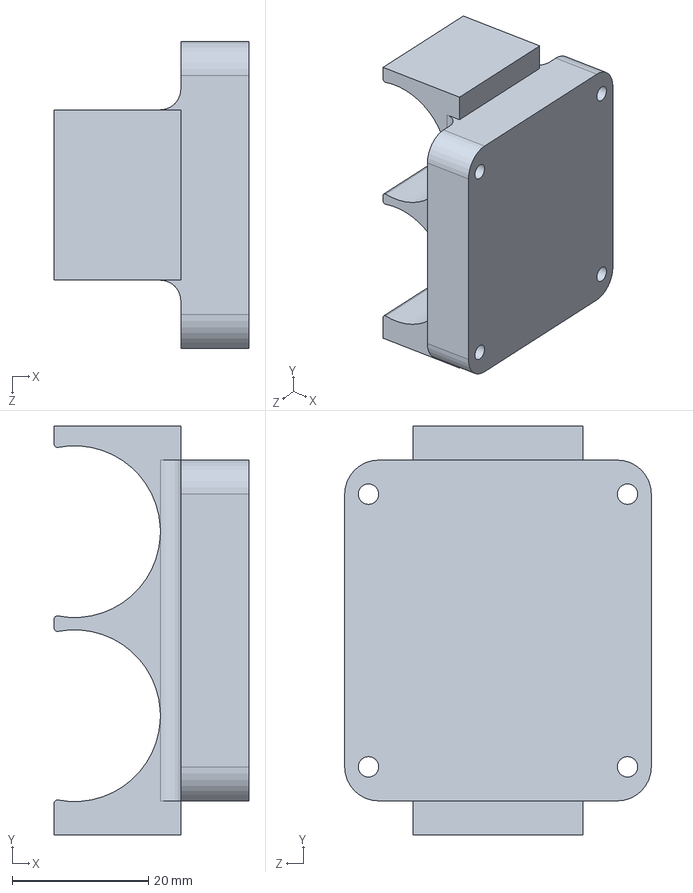
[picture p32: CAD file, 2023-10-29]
Solidworks CAD files/Sealed 3DP Box (for electronics) with screen, knob, pumps/Dual 12V pump holder.SLDPRT
28.6 x 60.0 x 45.0 mm

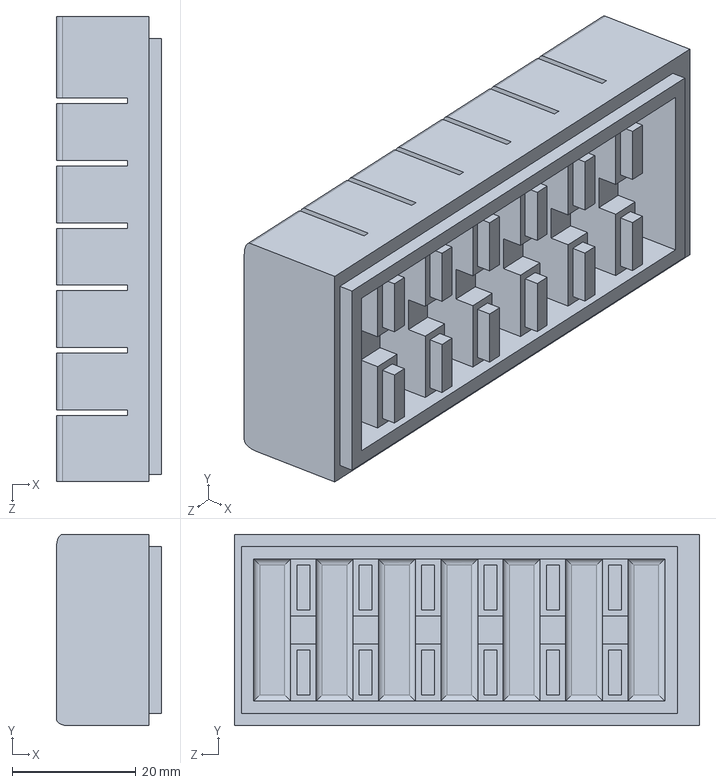
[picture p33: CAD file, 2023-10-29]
Solidworks CAD files/PneuNet 'Finger' Actuator/PneuNet Finger (positive) without base attached - for reference only.SLDPRT
17.0 x 31.0 x 75.3 mm

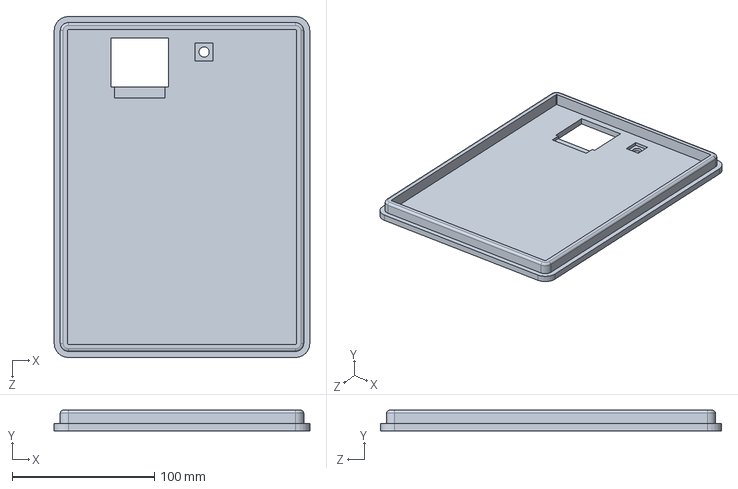
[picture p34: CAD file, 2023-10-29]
Solidworks CAD files/Sealed 3DP Box (for electronics) with screen, knob, pumps/LId to electronics Enclosure box.SLDPRT
180.0 x 14.5 x 240.0 mm

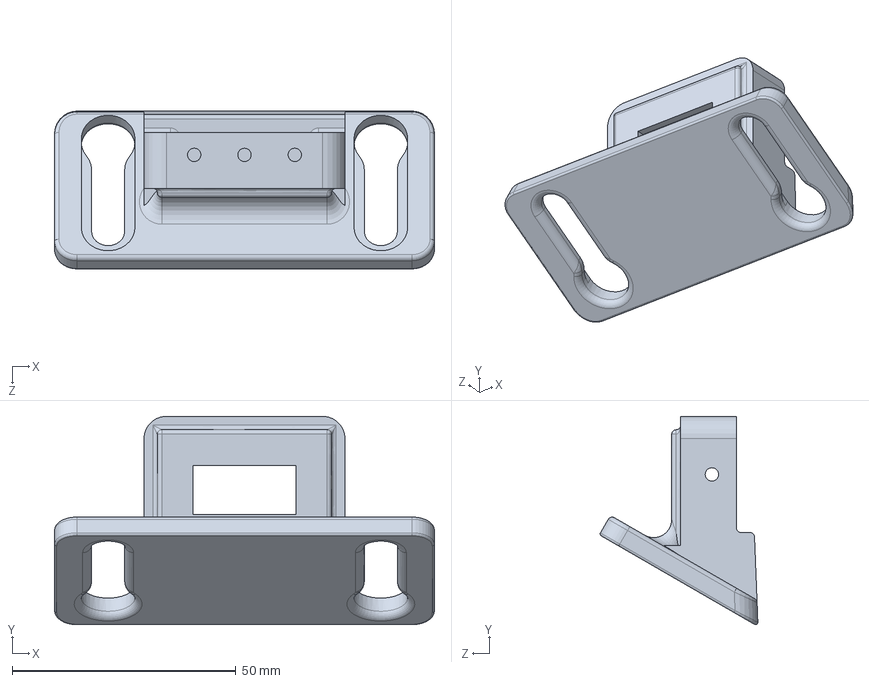
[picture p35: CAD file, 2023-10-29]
Solidworks CAD files/PneuNet 'Finger' Actuator/Attachment to board for end pneunet finger actuator.SLDPRT
85.0 x 46.6 x 35.3 mm

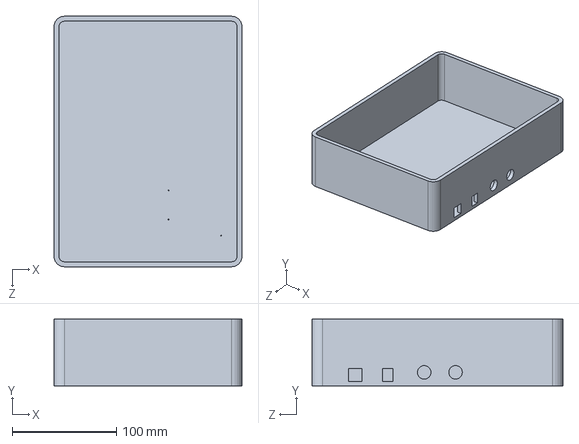
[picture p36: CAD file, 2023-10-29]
Solidworks CAD files/Sealed 3DP Box (for electronics) with screen, knob, pumps/Base to Electronics enclosure box.SLDPRT
180.0 x 64.0 x 240.0 mm

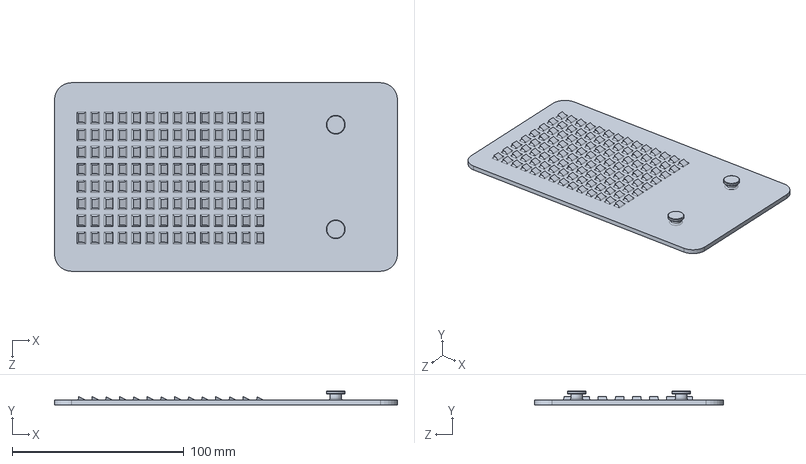
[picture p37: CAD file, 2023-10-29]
Solidworks CAD files/PneuNet 'Finger' Actuator/Chopping board base (with texture and keyhole mount).SLDPRT
200.0 x 8.40 x 110.0 mm

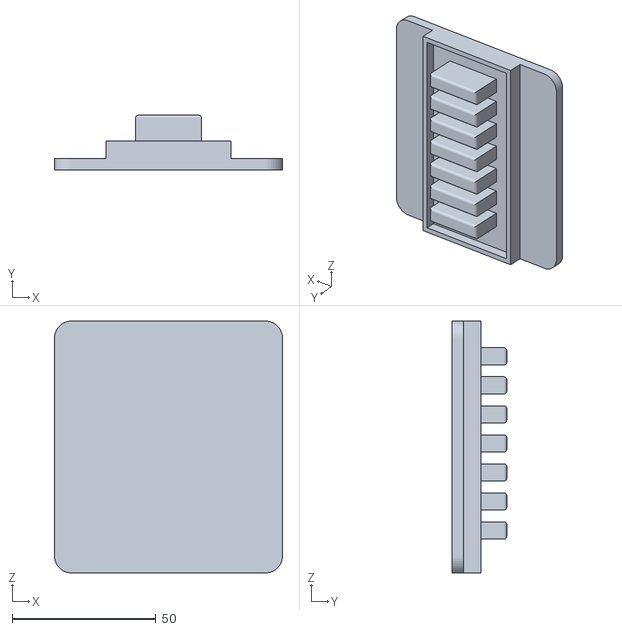
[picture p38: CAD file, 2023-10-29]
Printable files (STL)/Mold soft actuator - bottom.STL
79.4 x 19.0 x 87.7

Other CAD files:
Solidworks CAD files/Sealed 3DP Box (for electronics) with screen, knob, pumps/Accessible Knob.SLDPRT
Printable files (STL)/Syringe Clamp JAW side.STL
Printable files (STL)/LId to electronics Enclosure.STL
Printable files (STL)/Attachment for end of PneuNet finger actuator - smaller.STL
Printable files (STL)/(PROTOYPE) Origami soft linear extension Mold.STL
Printable files (STL)/Base to Electronics enclosure.STL
Printable files (STL)/Chopping Board base - finger actuator.STL
Printable files (STL)/Dual Air Pump holder.STL
Printable files (STL)/Syringe holder (holds both syringes to board).STL
Solidworks CAD files/PneuNet 'Finger' Actuator/(Prototype) PneuNet longer length - top section.SLDPRT
Solidworks CAD files/PneuNet 'Finger' Actuator/PneuNet mould - top section.SLDPRT

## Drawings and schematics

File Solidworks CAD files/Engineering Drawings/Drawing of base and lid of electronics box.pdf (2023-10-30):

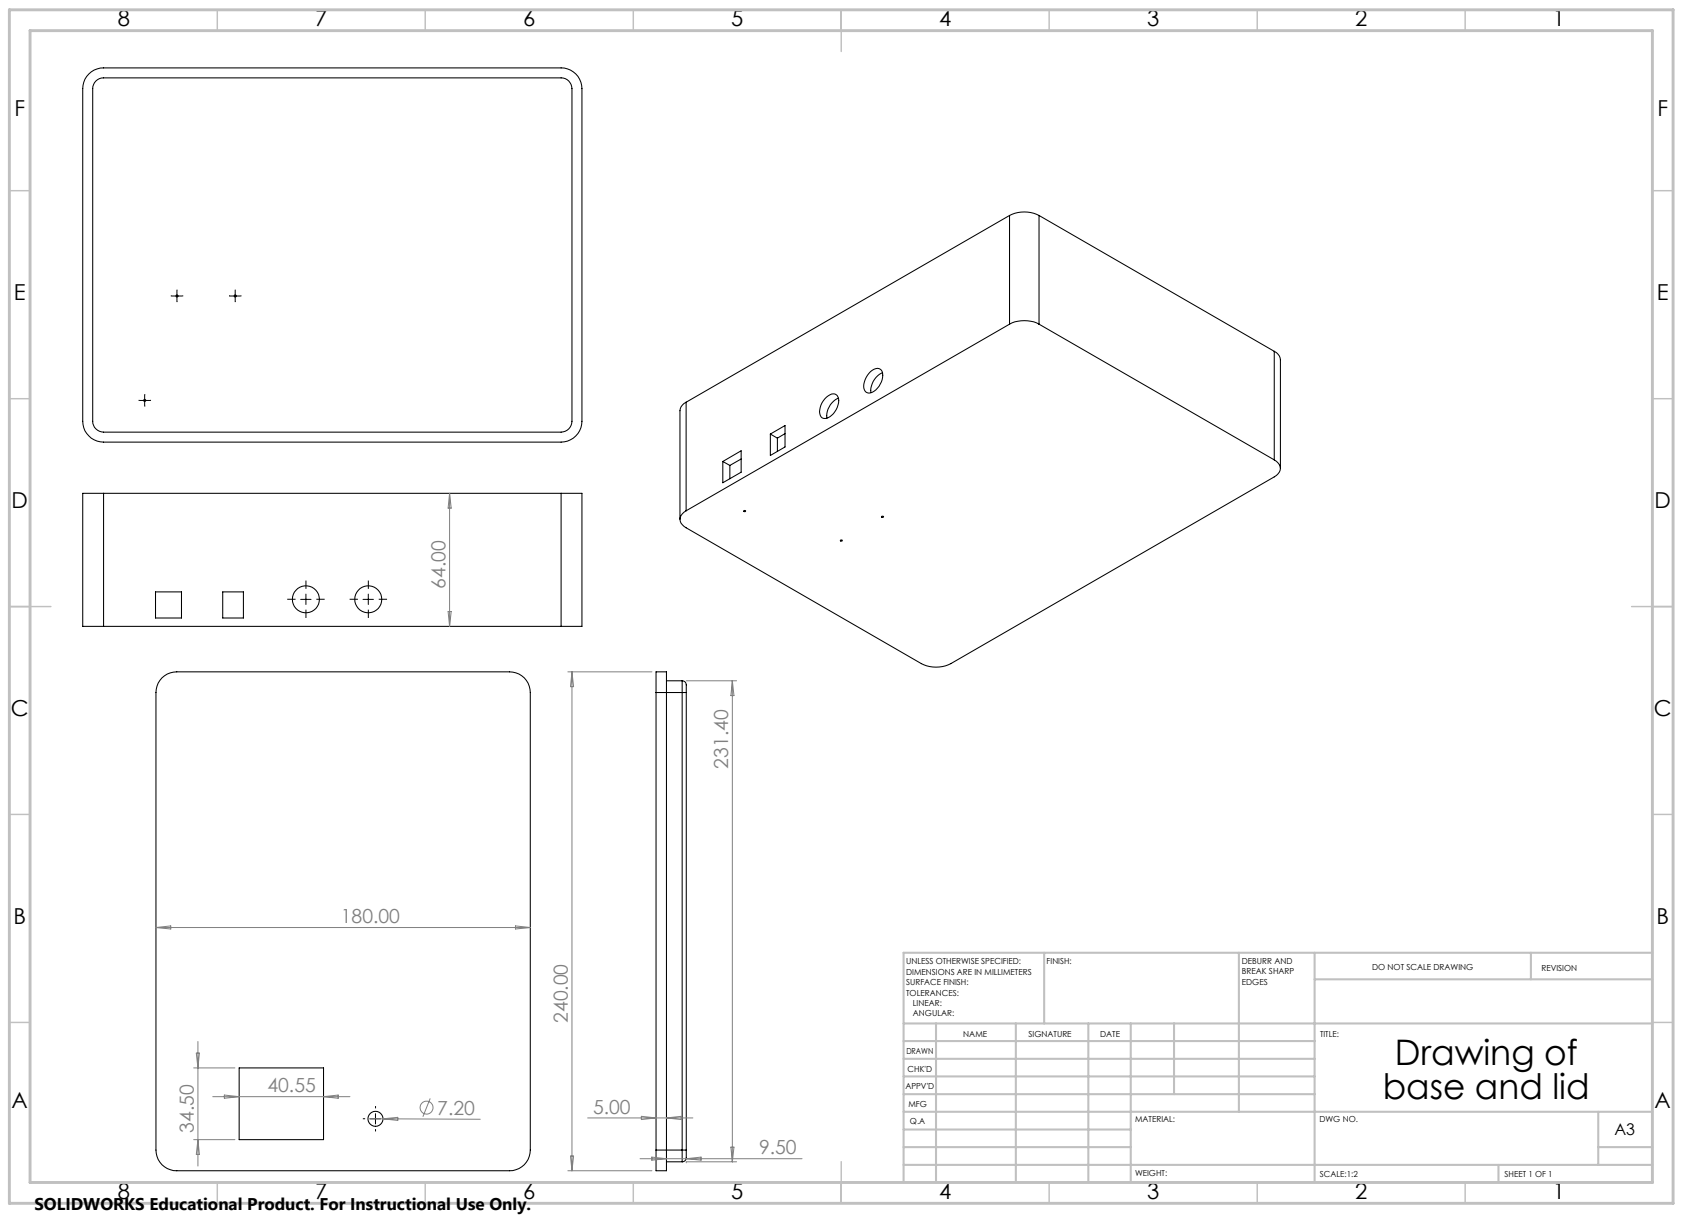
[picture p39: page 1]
FINISH:; DEBURR AND; BREAK SHARP; DO NOT SCALE DRAWING; REVISION; SCALE:1:2; SHEET 1 OF 1; base and lid

UNLESS OTHERWISE SPECIFIED:
DIMENSIONS ARE IN MILLIMETERS
SURFACE FINISH:
TOLERANCES:
LINEAR:
ANGULAR:

NAME | SIGNATURE | DATE | | | | TITLE: Drawing of

DRAWN
CHK'D
APPV'D
MFG
Q.A | | | | MATERIAL: | DWG NO. | A3

SOLIDWORKS Educational Product. For Instructional Use Only.

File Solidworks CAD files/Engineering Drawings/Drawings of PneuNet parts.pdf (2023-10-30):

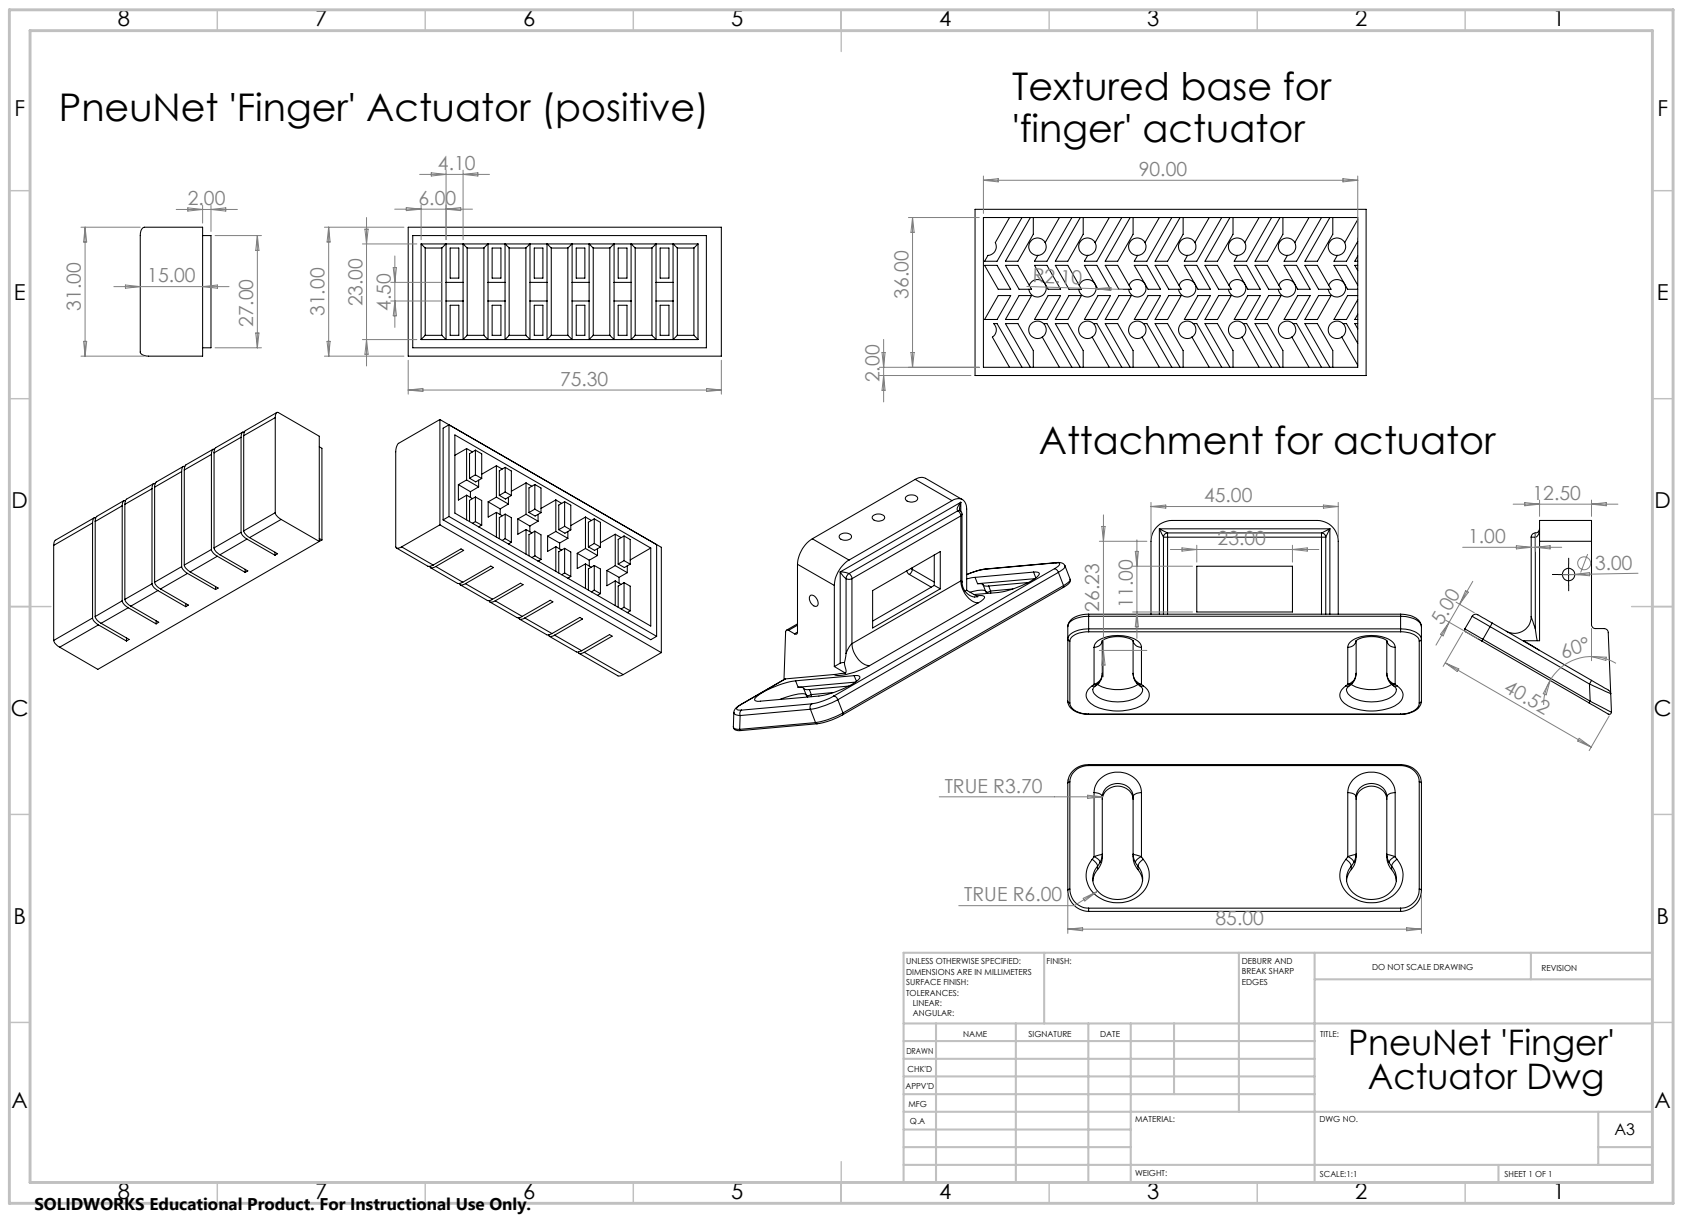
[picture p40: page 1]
TRUE R6.00; TRUE R3.70; PneuNet 'Finger' Actuator (positive); Textured base for; 'finger' actuator; FINISH:; DEBURR AND; BREAK SHARP; DO NOT SCALE DRAWING; REVISION; SCALE:1:1; SHEET 1 OF 1; Actuator Dwg A

Attachment for actuator

UNLESS OTHERWISE SPECIFIED:
DIMENSIONS ARE IN MILLIMETERS
SURFACE FINISH:
TOLERANCES:
LINEAR:
ANGULAR:

NAME | SIGNATURE | DATE | | | | PneuNet 'Finger' TITLE:

DRAWN
CHK'D
APPV'D
MFG
Q.A | | | | MATERIAL: | DWG NO. | A3

SOLIDWORKS Educational Product. For Instructional Use Only.

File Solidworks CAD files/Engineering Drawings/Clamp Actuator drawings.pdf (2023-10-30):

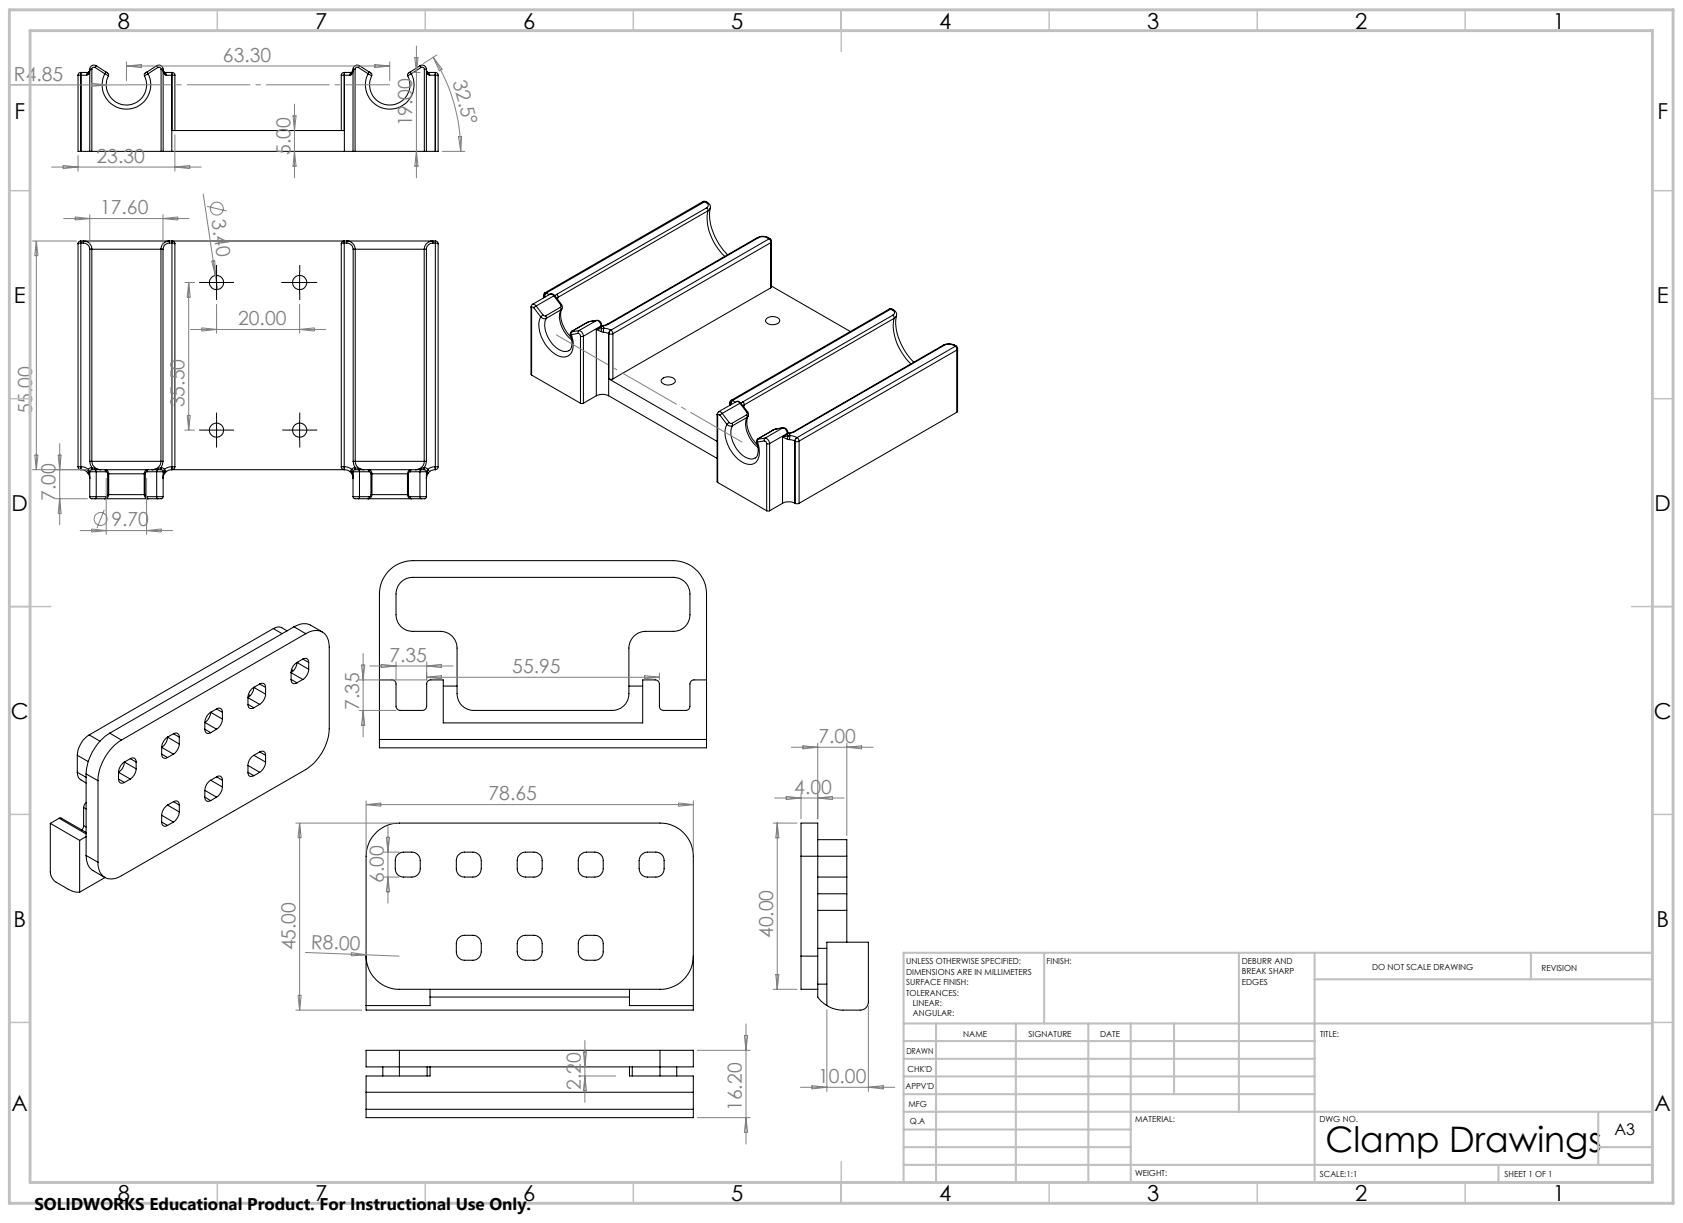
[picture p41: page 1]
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

UNLESS OTHERWISE SPECIFIED:
DIMENSIONS ARE IN MILLIMETERS
SURFACE FINISH:
TOLERANCES:
LINEAR:
ANGULAR:

NAME | SIGNATURE | DATE | | | | TITLE:

DRAWN
CHK'D
APPV'D
MFG
Q.A | | | | MATERIAL: | DWG NO. Clamp Drawings | A3

SOLIDWORKS Educational Product. For Instructional Use Only.

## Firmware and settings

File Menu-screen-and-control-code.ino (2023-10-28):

//////////////////////////////////////////////
//       Arduino Rotary Encoder Menu        //
//                 v1.0                     //
//           http://www.educ8s.tv           //
/////////////////////////////////////////////

#include <Adafruit_GFX.h>
#include <Adafruit_PCD8544.h>
#include <ClickEncoder.h>
#include <TimerOne.h>

// ------------------------------- pin mapping -------------------------------//
Adafruit_PCD8544 display = Adafruit_PCD8544(13, 12, 8, 7, 6);
// Rotary Encoder Inputs
#define CLK 2
#define DT 3
#define SW 4

// Mosfet PWM outputs
#define SOL1 5  //solenoid
#define SOL2 7
#define PUMP1 8  //air pump 1
#define PUMP2 9  //air pump 2

// Pressure Sensor
#define PRS1_LOG A0  // Honeywell basic sensor
#define PRS2_LOG A5  // ditto + 1

// Force Sensor
#define FSR1 A3  // Is also connected to GND and 10K ohm resistor
#define FSR2 A4

// ---------------------------- sensor variables -----------------------------//
// Force Sensitive Resistor
const int FSRmax = 50;      // the point where there is nothing touching the resistor
const int FSRminForce = 9;  // The point where the force sensor 'bottoms out'
int FSRval1;
int currentFSR1;
int lastFSR1;
int mappedFSR1;
int FSRval2;
int currentFSR2;
int lastFSR2;
int mappedFSR2;

// Pressure Sensor
const int PRSmax = 50;  // the point where there is nothing touching the resistor
int PRSVal1;
int currentPRS1;
int lastPRS1 = 0;
int mappedPRS1;
int PRSVal2;
int currentPRS2;
int lastPRS2 = 0;
int mappedPRS2;
// what the raw value from the sensor will be added to to give the final value.
const int PRS1_intercept = -165;
const int PRS2_intercept = -165;
// ---------------------------- display variables ----------------------------//
int menuitem = 1;
int frame = 1;
int page = 1;
int lastMenuItem = 1;

//Main Menu items
String menuItem1 = "Hardness Mode";
String menuItem2 = "Device Select";
String menuItem3 = "Sensors";
String menuItem4 = "Manual";
String menuItem5 = "Backlight: ON";
String menuItem6 = "Reset";
String menuItem7 = "Power OFF";
// Sub/Page 3 menu items
String subMenuItem3a = "Force Sensors";
String subMenuItem3b = "Pressure:";


// Menu 1: Hardness Mode
String HardnessMode[3] = { "Onion", "Carrot", "Tomato" };
int selectedHardnessMode = 0;

// Menu 2: Device Select
String Device[2] = { "Finger", "Clamp" };
int selectedDevice = 0;

// Menu 3: Sensors
String sensorVar1 = "Finger";
String sensorVar2 = "Clamp";

// Menu 4+:
boolean backlight = true;
boolean powerVar = false;
const int contrast = 60;

boolean up = false;
boolean down = false;
boolean middle = false;

ClickEncoder *encoder;
int16_t last, value;


// ---------------------------- void setup ---------------------------- //
void setup() {
  // Solnoid Output pins for MOSFET baord
  pinMode(SOL1, OUTPUT);
  pinMode(SOL2, OUTPUT);
  // Pump Outputs for PWM
  pinMode(PUMP1, OUTPUT);
  pinMode(PUMP2, OUTPUT);

  // display set up
  pinMode(9, OUTPUT);
  turnBacklightOn();
  display.begin();
  display.clearDisplay();
  display.setContrast(contrast);
  display.display();

  // encoder set up
  encoder = new ClickEncoder(CLK, DT, SW);
  encoder->setAccelerationEnabled(false);

  Timer1.initialize(1000);
  Timer1.attachInterrupt(timerIsr);

  last = encoder->getValue();
  display.setRotation(2);

  // Setup Serial Monitor
  Serial.begin(9600);
}

// ---------------------------- void loop ---------------------------- //
void loop() {

  drawMenu();

  readRotaryEncoder();
  ClickEncoder::Button b = encoder->getButton();
  if (b != ClickEncoder::Open) {
    switch (b) {
      case ClickEncoder::Clicked:
        middle = true;
        break;
    }
  }
  MenuCode();  // All display, menu settings etc.
  ForceSensor();
  PressureSensor();

  Serial.print("PRS1:");
  Serial.print(PRSVal1);
  Serial.print(",");
  Serial.print("PRS2:");
  Serial.print(PRSVal2);
  Serial.println(",");
}

// ------------------------ Sensor Value Gathering Code ---------------------- //

void PressureSensor() {
  currentPRS1 = analogRead(PRS1_LOG);
  if (currentPRS1 != lastPRS1) {
    PRSVal1 = ((analogRead(PRS1_LOG) * 1.6) + PRS1_intercept) * 0.1;
    delay(10);
  }
  lastPRS1 = currentPRS1;

  currentPRS2 = analogRead(PRS2_LOG);
  if (currentPRS2 != lastPRS2) {
    PRSVal2 = ((analogRead(PRS2_LOG) * 1.6) + PRS2_intercept) * 0.1;
    delay(10);
  }
  lastPRS2 = currentPRS2;
  delay(100);
}

void ForceSensor() {
  currentFSR1 = analogRead(FSR1);
  if (currentFSR1 != lastFSR1) {
    FSRval1 = map(analogRead(FSR1), FSRminForce, 1024, 0, (FSRmax + 1));
    delay(10);
    //Serial.print("Force Sensor Value:");
    // Serial.print(FSRval1);
    //Serial.println(",");
  }
  lastFSR1 = currentFSR1;
  delay(1);

  currentFSR2 = analogRead(FSR2);
  if (currentFSR2 != lastFSR2) {
    FSRval2 = map(analogRead(FSR2), FSRminForce, 1024, 0, (FSRmax + 1));
    delay(10);
    // Serial.print("Force Sensor Value2:");
    // Serial.print(FSRval2);
    // Serial.println(",");
  }
  lastFSR2 = currentFSR2;
  delay(1);
}

// -------------------------- All Menu/Display Code -------------------------- //
void MenuCode() {

  if (up && page == 1) {

    up = false;
    if (menuitem == 2 && frame == 2) {
      frame--;
    }
    if (menuitem == 3 && frame == 3) {
      frame--;
    }
    if (menuitem == 4 && frame == 4) {
      frame--;
    }
    if (menuitem == 5 && frame == 5) {
      frame--;
    }
    lastMenuItem = menuitem;
    menuitem--;
    if (menuitem == 0) {
      menuitem = 1;
    }
  } else if (up && page == 2 && menuitem == 1) {
    up = false;
    selectedHardnessMode--;
    if (selectedHardnessMode == -1) {
      selectedHardnessMode = 2;
    }
  } else if (up && page == 2 && menuitem == 2) {
    up = false;
    selectedDevice--;
    if (selectedDevice == -1) {
      selectedDevice = 1;
    }
  } else if (up && page == 2 && menuitem == 3) {
    up = false;
    // insert code
  } else if (up && page == 2 && menuitem == 4) {
    up = false;
    //insert code to do
  }

  if (down && page == 1)  //We have turned the Rotary Encoder Clockwise
  {

    down = false;
    if (menuitem == 3 && lastMenuItem == 2) {
      frame++;
    } else if (menuitem == 4 && lastMenuItem == 3) {
      frame++;
    } else if (menuitem == 5 && lastMenuItem == 4 && frame != 5) {
      frame++;
    } else if (menuitem == 5 && lastMenuItem == 4 && frame != 5) {
      frame++;
    } else if (menuitem == 6 && lastMenuItem == 5 && frame != 5) {
      frame++;
    }
    lastMenuItem = menuitem;
    menuitem++;
    if (menuitem == 8) {
      menuitem--;
    }

  } else if (down && page == 2 && menuitem == 1) {
    down = false;
    selectedHardnessMode++;
    if (selectedHardnessMode == 3) {
      selectedHardnessMode = 0;
    }
  } else if (down && page == 2 && menuitem == 2) {
    down = false;
    selectedDevice++;
    if (selectedDevice == 2) {
      selectedDevice = 0;
    }
  } else if (down && page == 2 && menuitem == 3) {
    down = false;
    // selectedLanguage++;
    // if(selectedLanguage == 3)
    // {
    //   selectedLanguage = 0;
    // }
  } else if (down && page == 2 && menuitem == 5) {
    down = false;
  }

  if (middle)  //Middle Button is Pressed
  {
    middle = false;

    if (page == 1 && menuitem == 5)  // Backlight Control
    {
      if (backlight) {
        backlight = false;
        menuItem5 = "Backlight OFF";
        turnBacklightOff();
      } else {
        backlight = true;
        menuItem5 = "Backlight: ON";
        turnBacklightOn();
      }
    }
    if (page == 2 && menuitem == 3) {
      page = 3;
    } else if (page == 3 && menuitem == 3) {
      page = 1;
    } else if (page == 1 && menuitem == 3) {
      page = 2;
    }
    if (page == 1 && menuitem == 6)  // Reset
    {
      resetDefaults();
    }
    if (page == 1 && menuitem == 7)  // PowerOff sequence
    {
      powerOff();
    }

    else if (page == 1 && menuitem <= 4 && menuitem != 3) {
      page = 2;
    } else if (page == 2 && menuitem != 3) {
      page = 1;
    }
  }
}
void drawMenu() {

  if (page == 1) {
    display.setTextSize(1);
    display.clearDisplay();
    display.setTextColor(BLACK, WHITE);
    display.setCursor(15, 0);
    display.print("MAIN MENU");
    display.drawFastHLine(0, 10, 83, BLACK);

    if (menuitem == 1 && frame == 1) {
      displayMenuItem(menuItem1, 15, true);
      displayMenuItem(menuItem2, 25, false);
      displayMenuItem(menuItem3, 35, false);
    } else if (menuitem == 2 && frame == 1) {
      displayMenuItem(menuItem1, 15, false);
      displayMenuItem(menuItem2, 25, true);
      displayMenuItem(menuItem3, 35, false);
    } else if (menuitem == 3 && frame == 1) {
      displayMenuItem(menuItem1, 15, false);
      displayMenuItem(menuItem2, 25, false);
      displayMenuItem(menuItem3, 35, true);
    }

    else if (menuitem == 2 && frame == 2) {
      displayMenuItem(menuItem2, 15, true);
      displayMenuItem(menuItem3, 25, false);
      displayMenuItem(menuItem4, 35, false);
    } else if (menuitem == 4 && frame == 2) {
      displayMenuItem(menuItem2, 15, false);
      displayMenuItem(menuItem3, 25, false);
      displayMenuItem(menuItem4, 35, true);
    } else if (menuitem == 3 && frame == 2) {
      displayMenuItem(menuItem2, 15, false);
      displayMenuItem(menuItem3, 25, true);
      displayMenuItem(menuItem4, 35, false);
    } else if (menuitem == 2 && frame == 2) {
      displayMenuItem(menuItem2, 15, true);
      displayMenuItem(menuItem3, 25, false);
      displayMenuItem(menuItem4, 35, false);
    }

    else if (menuitem == 3 && frame == 3) {
      displayMenuItem(menuItem3, 15, true);
      displayMenuItem(menuItem4, 25, false);
      displayMenuItem(menuItem5, 35, false);
    } else if (menuitem == 4 && frame == 3) {
      displayMenuItem(menuItem3, 15, false);
      displayMenuItem(menuItem4, 25, true);
      displayMenuItem(menuItem5, 35, false);
    } else if (menuitem == 5 && frame == 3) {
      displayMenuItem(menuItem3, 15, false);
      displayMenuItem(menuItem4, 25, false);
      displayMenuItem(menuItem5, 35, true);
    }

    else if (menuitem == 4 && frame == 4) {
      displayMenuItem(menuItem4, 15, true);
      displayMenuItem(menuItem5, 25, false);
      displayMenuItem(menuItem6, 35, false);
    } else if (menuitem == 5 && frame == 4) {
      displayMenuItem(menuItem4, 15, false);
      displayMenuItem(menuItem5, 25, true);
      displayMenuItem(menuItem6, 35, false);
    } else if (menuitem == 6 && frame == 4) {
      displayMenuItem(menuItem4, 15, false);
      displayMenuItem(menuItem5, 25, false);
      displayMenuItem(menuItem6, 35, true);
    }

    else if (menuitem == 5 && frame == 5) {
      displayMenuItem(menuItem5, 15, true);
      displayMenuItem(menuItem6, 25, false);
      displayMenuItem(menuItem7, 35, false);
    } else if (menuitem == 6 && frame == 5) {
      displayMenuItem(menuItem5, 15, false);
      displayMenuItem(menuItem6, 25, true);
      displayMenuItem(menuItem7, 35, false);
    } else if (menuitem == 7 && frame == 5) {
      displayMenuItem(menuItem5, 15, false);
      displayMenuItem(menuItem6, 25, false);
      displayMenuItem(menuItem7, 35, true);
    }

    display.display();
  } else if (page == 2 && menuitem == 1) {
    displayStringMenuPage(menuItem1, HardnessMode[selectedHardnessMode]);
  }

  else if (page == 2 && menuitem == 2) {
    displayStringMenuPage(menuItem2, Device[selectedDevice]);
  } else if (page == 2 && menuitem == 3) {
    displayTwoIntMenuPage(subMenuItem3a, FSRval1, FSRval2, sensorVar1, sensorVar2);

  } else if (page == 3 && menuitem == 3) {
    displayTwoIntMenuPage(subMenuItem3b, PRSVal1, PRSVal2, sensorVar1, sensorVar2);
  }

  else if (page == 2 && menuitem == 4) {
    //displayStringMenuPage(menuItem4, difficulty[selectedDifficulty]);
  } else if (page == 2 && menuitem == 5) {
    //displayStringMenuPage(menuItem5
  }
}


void resetDefaults() {
  selectedHardnessMode = 0;
  selectedDevice = 0;
  backlight = true;
  powerVar = false;
  backlight = true;
  menuItem5 = "Backlight: ON";
}

void powerOff() {
  turnBacklightOff();
  //have systems here like turn off all pumps, have solenoids open
  powerVar = true;
}

void turnBacklightOn() {
  digitalWrite(9, HIGH);
}

void turnBacklightOff() {
  digitalWrite(9, LOW);
}

void displayTwoIntMenuPage(String menuItem, int value1, int value2, String Var1, String Var2) {
  display.setTextSize(1);
  display.clearDisplay();
  display.setTextColor(BLACK, WHITE);
  display.setCursor(3, 0);
  display.print(menuItem);
  display.drawFastHLine(0, 10, 83, BLACK);
  display.setTextSize(0.8);
  display.setCursor(0, 15);
  display.print(Var1);
  display.setCursor(45, 15);
  display.print(Var2);
  display.drawFastVLine(41, 12, 50, BLACK);
  display.setTextSize(2);
  display.setCursor(4, 27);
  display.print(value1);
  display.setCursor(46, 27);
  display.print(value2);
  display.display();
}
void displayOneIntMenuPage(String menuItem, int value) {
  display.setTextSize(1);
  display.clearDisplay();
  display.setTextColor(BLACK, WHITE);
  display.setCursor(5, 0);
  display.print(menuItem);
  display.drawFastHLine(0, 10, 83, BLACK);
  display.setCursor(5, 15);
  display.print("Value");
  display.setTextSize(2);
  display.setCursor(5, 25);
  display.print(value);
  display.setTextSize(2);
  display.display();
}

void displayStringMenuPage(String menuItem, String value) {
  display.setTextSize(1);
  display.clearDisplay();
  display.setTextColor(BLACK, WHITE);
  display.setCursor(3, 0);
  display.print(menuItem);
  display.drawFastHLine(0, 10, 83, BLACK);
  // display.setCursor(5, 15);
  // display.print("Selection");
  display.setTextSize(2);
  display.setCursor(5, 15);
  display.print(value);
  display.setTextSize(2);
  display.display();
}

void displayMenuItem(String item, int position, boolean selected) {
  if (selected) {
    display.setTextColor(WHITE, BLACK);
  } else {
    display.setTextColor(BLACK, WHITE);
  }
  display.setCursor(0, position);
  display.print(">" + item);
}

void timerIsr() {
  encoder->service();
}

void readRotaryEncoder() {
  value += encoder->getValue();

  if (value / 2 > last) {
    last = value / 2;
    down = true;
    delay(150);
  } else if (value / 2 < last) {
    last = value / 2;
    up = true;
    delay(150);
  }
}

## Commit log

2023-10-29 Added Solidworks CAD files
    [(PROTOTYPE) Mould for origami soft linear extension actuator.SLDPRT, (Prototype) PneuNet longer length - BASE section.SLDPRT, (Prototype) PneuNet longer length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]
2023-10-29 Upload Printable files
    [(PROTOYPE) Origami soft linear extension Mold.STL, Attachment for end of PneuNet finger actuator - smaller.STL, Base to Electronics enclosure.STL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]
